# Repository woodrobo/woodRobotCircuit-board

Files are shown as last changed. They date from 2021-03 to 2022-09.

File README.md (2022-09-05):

# woodRobotCircuit-board
趣味でロボコン的なロボットを動かす回路を作ろうプロジェクト（？）の回路・基板リポジトリである。ファームウェアは[ここ](https://github.com/woodrobo/woodRobotCircuit-firmware/tree/kanojo_robo)。
ロボコンや趣味のロボット製作等の参考にどうぞ。  

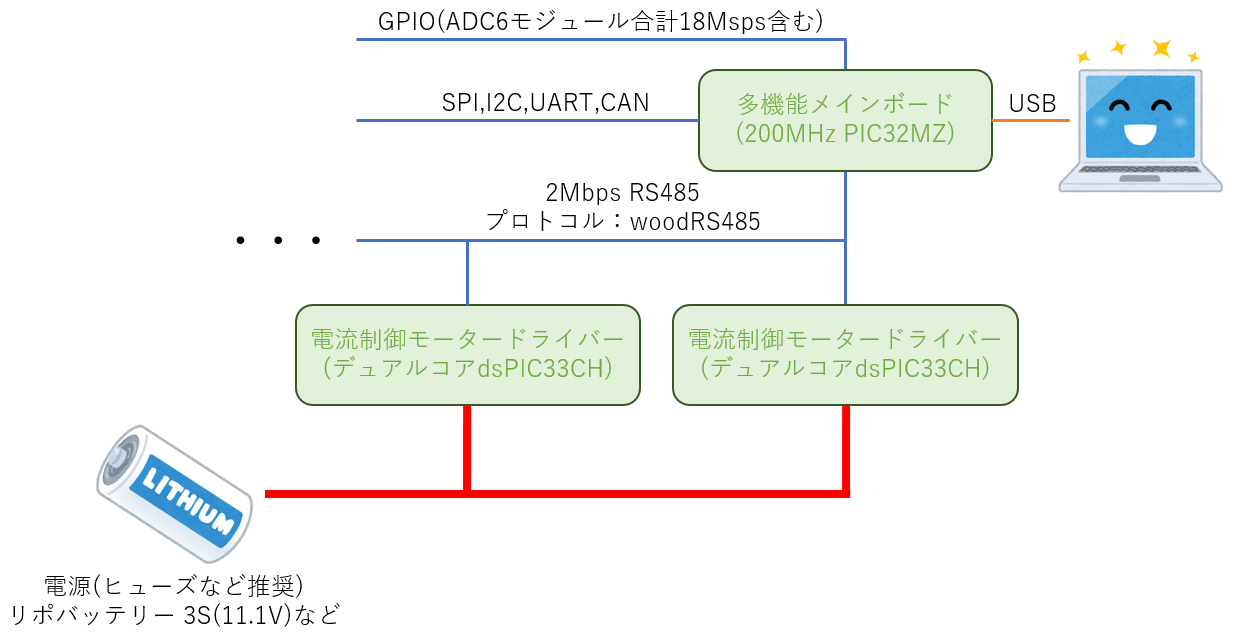
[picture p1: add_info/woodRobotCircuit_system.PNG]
システム概要
  
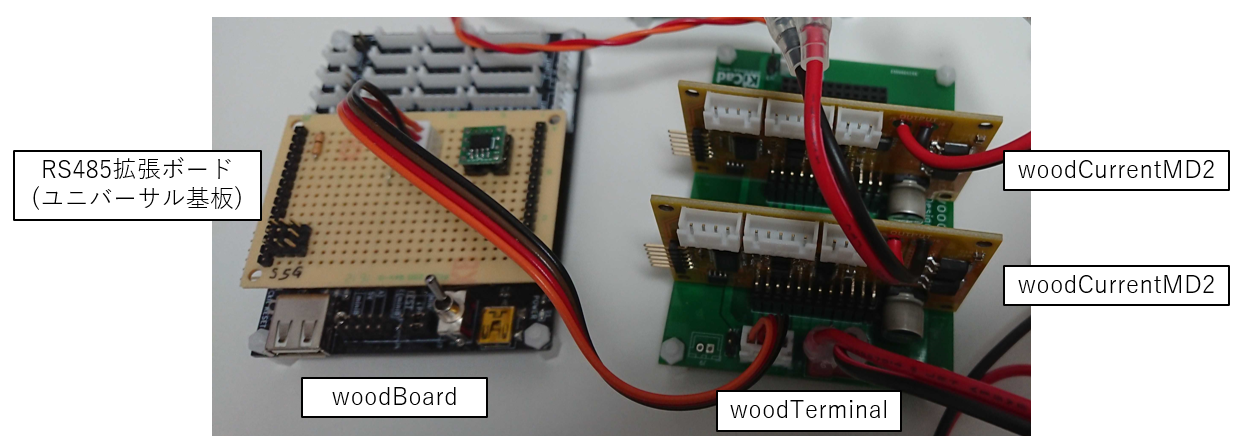
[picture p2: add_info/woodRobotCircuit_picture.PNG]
実際の基板たち
  

メインボードとモータードライバは2MbpsのRS485で接続されており、プロトコルはwoodRS485という独自規格を用いているが、これも[リポジトリ](https://github.com/woodrobo/wood_rs485)として公開されており、C言語が使用できるマイコンであればどのマイコンでも移植できるよう実装されている。  
モータードライバーは電流制御に対応しており高度な制御が可能となる。  

# 電流制御とは
モーターは一般に抵抗とコイル、そして回転速度に比例する逆起電力の3つが直列接続されたモデルで表現されます。  

$$ Vin = Ri + L\frac{di}{dt}+V$$

電子工作でよく使用されるPWM制御ではこの3つの要素全体にかける電圧を制御しているのでこれは直接的に物理的な意味を持ちません。モーターに流れる電流はトルクに比例すると言われこの電流を制御する電流制御方式ではトルクという物理量を直接的に扱うことができます。

$$ \tau = K_t i $$

製品や研究の世界ではこのトルク制御により運動方程式からモデルを立てて制御をすることが一般となっています。例えばロボティクスでは動力学や逆動力学によりロボットアームを制御しています。モデルに基づいた制御をするために電流制御は必須の機能です。

# 基板の簡単な紹介
woodBoard  
メインボードでありRS485以外にもSPI,I2C,UART,CANなどの通信ポートを備えている。また余った全てのGPIOをピンソケットに出しており、3MbpsのADCモジュールが6つ搭載されているため合計で18Mspsもの高速なAD変換を実現できる。もちろんこれはモジュール数であるのでAD変換可能なピン数はこれより多い。

woodTerminal  
モータードライバー基板などをまとめるための基板であり、1つのターミナル基板につきモータードライバー基板を5枚配置することができる。制御側の電源はRS485ポートの5V電源のほか、DCDCコンバータが搭載されているのでLiPo 3S(11.1V)等からも5Vを生成できる。
  
woodCurrentMD  
初期のモータードライバーであるが、ゲートドライバICが手に入らなかったことや回路トラブルにより闇の基板だぞ。

woodCurrentMD2  
20kHz電流制御モータードライバー。ロジック側とパワー側はフォトカプラで絶縁されており、モーター電流は磁気式の電流センサで計測している。UARTポート、エンコーダポート、ADCポートを搭載しており、また搭載しているマイコンはマルチプレクサにより自由にピン配置を変更できるため拡張性に優れる。180MHz/200MHzデュアルコアマイコンdsPIC33CHにより電流制御とその他処理をコアで分離するためプログラムの拡張性に優れる。  

# 基板発売について  
ここのサイトで基板のみを売ってるぞ！  
https://woodrobo.booth.pm/items/4136212

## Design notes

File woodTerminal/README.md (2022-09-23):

# woodTerminal
モータードライバーなどを5枚までまとめるターミナル基板

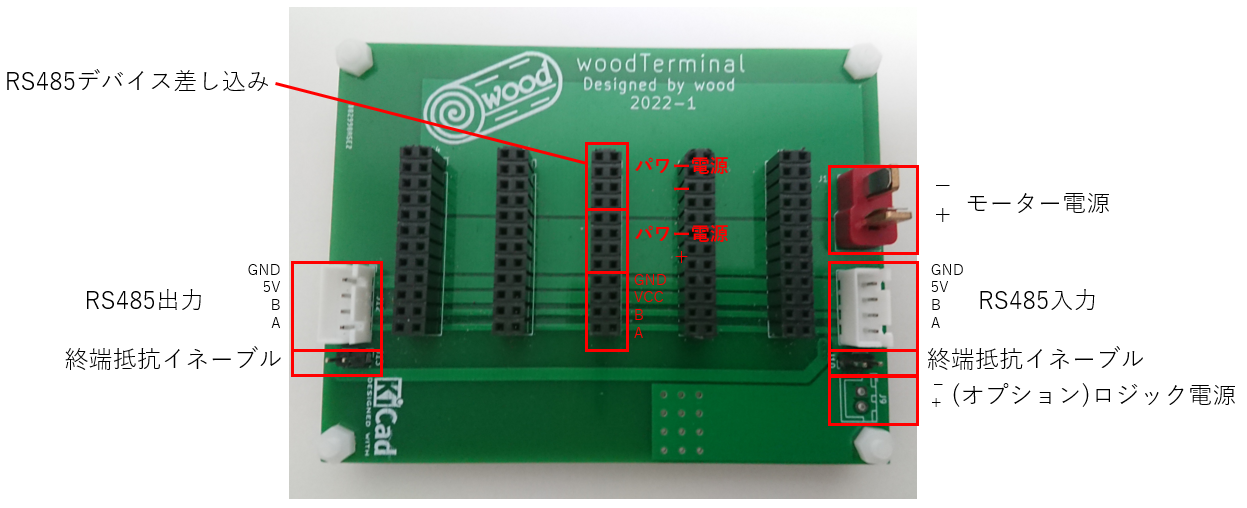
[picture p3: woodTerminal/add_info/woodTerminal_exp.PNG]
基板表

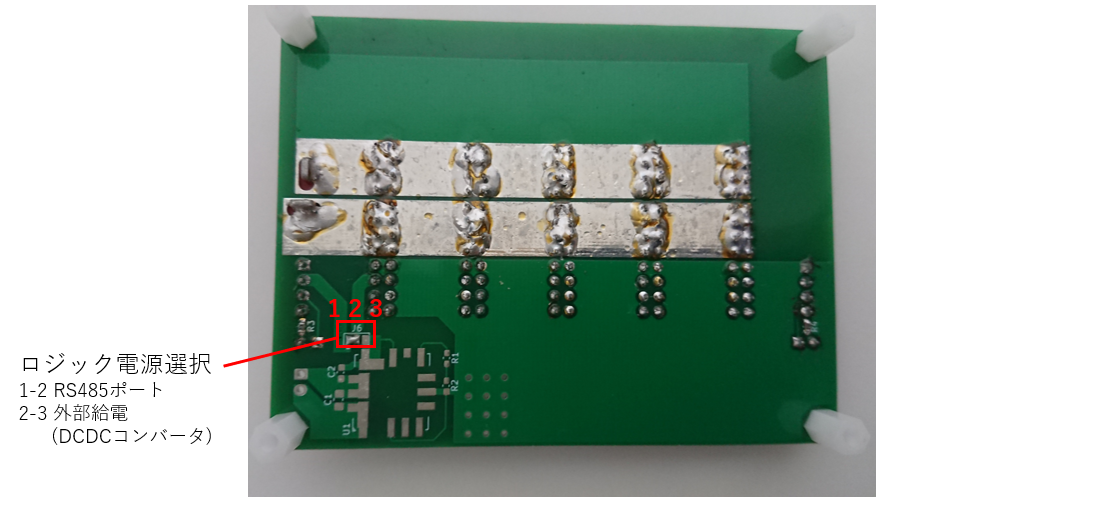
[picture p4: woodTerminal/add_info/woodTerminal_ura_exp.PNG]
基板裏
 

仕様
- ロジック側
	- RS485の4ピンポート(A,B,5V,GND)
		- RS485の終端抵抗は横にあるピンヘッダをショートすることで行う
	- 外部電源供給
		- LiPo3S(11.1V)などからDCDCコンバータを通して5Vを供給する(オプション)
	- 電源選択は基板裏面にあるパッドをショートして行う(4ピンコネクタor外部供給)
	- よく考えると外部供給は一度も試してない(ｶｽ)
- パワー側
	- Tコネクタ
  
  # 部品について  
  部品表.csvおよび部品個数表.csvを見てくれ。

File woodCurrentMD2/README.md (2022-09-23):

# woodCurrentMD2
2Mbps RS485対応電流制御DCモータードライバー

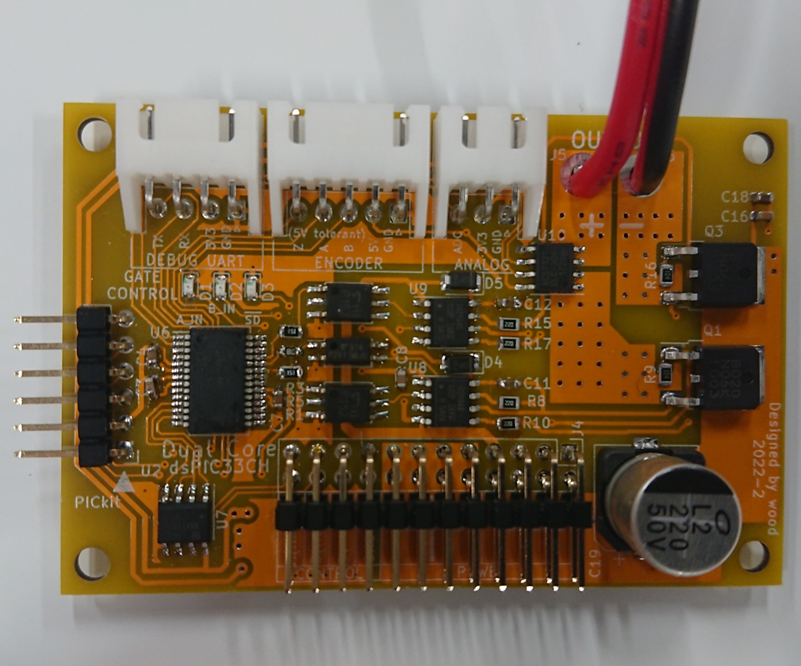
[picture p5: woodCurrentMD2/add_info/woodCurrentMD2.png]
基板表

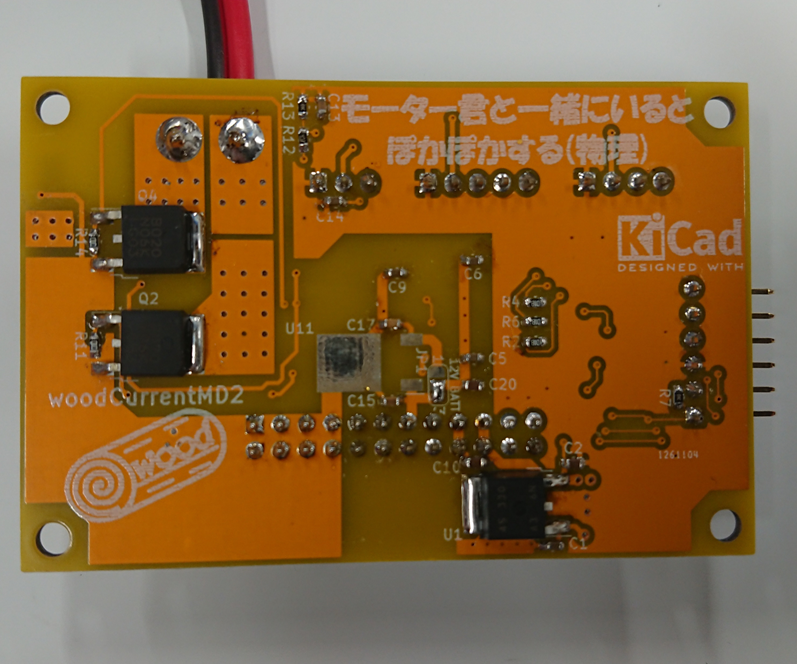
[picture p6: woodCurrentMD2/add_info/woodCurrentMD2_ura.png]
基板裏
  

仕様
- 通信規格2Mbps RS485
	- 受信：電圧制御(PWM値)、電流制御
	- 送信：電流値、AD変換ポートの値、エンコーダのカウント値
- woodTerminal接続端子
	- ロジック側とパワー側は絶縁されている
	- ロジック側：A, B, 5V, GND
	- パワー側　：VCC, GND
	- 詳細はwoodTerminalを参照の事
- 20kHz電流制御
- デバッグUARTポート
	- 現状RXから信号が出てる()
- インクリメンタル型エンコーダポート
	- PICのQEI機能でハードウェア処理
	- たぶん高速な波形も読める
	- Z相はファームウェアが現在対応してない、配線しないこと
- (ポテンショなどの)AD変換ポート

通信規格  
woodRS485で以下のデータをやり取りする。

**マイコンボード→モータードライバー**  
モードは0で電圧制御(PWM値)、1で電流制御を意味する。16bit値は16bitのsigned int型であり、電圧制御ではPWM値(-10000 ~ 10000)を指示し、電流制御では1当たり0.0179[A]となる。  
例えば、電圧制御PWM1000ならば「0,3,232」となる。電流制御1Aならば「1,0,56」(1.0024A)となる。

| バイト数 | データ |
----|---- 
| 1 | モード |
| 2 | 16bit値(上位バイト) |
| 3 | 16bit値(下位バイト) |

**モータードライバー→マイコンボード**  
電流値は16bitのsigned int型であり、1あたり0.0179[A]を意味する。AD変換ポートはAD変換値(12bit 0-4095)が入っている。 エンコーダは16bitのsigned int型である。(インクリメンタル型エンコーダは差分しか意味を持たないのでunsignedと解釈してもsignedと解釈しても同じ)

| バイト数 | データ |
----|---- 
| 1 | 電流値(上位バイト) |
| 2 | 電流値(下位バイト) |
| 3 | AD変換ポート(上位バイト) |
| 4 | AD変換ポート(下位バイト) |
| 5 | エンコーダ(上位バイト) |
| 6 | エンコーダ(下位バイト) |
  
  # 部品について  
  部品表.csvおよび部品個数表.csvを見てくれ。

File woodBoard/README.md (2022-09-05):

# woodBoard
ロボット回路のメインボード

趣味でロボコン的なロボットを動かす回路を作ろうプロジェクト（？）のメインボードである。  
PIC32MZを使用しており200MHz/330DMIPSらしい。（たぶん）  
woodBoardの特徴を説明すると  
- 通信ポートが豊富(アドレスが被っても安心設計)
    - CAN通信2ポート(各ポートに2つコネクタ搭載、終端抵抗ジャンパピンで設定可能)  
    - SPI通信2ポート(そのうち1つのポートはSS違いで4つコネクタ配置、もう1つはピンソケット)
    - I2C通信2ポート(そのうち1つのポートは4つコネクタ配置、もう1つはピンソケット)
    - UART5ポート(USBシリアルに1,通信ポートに2,ピンソケットに2)
- ほとんど秋月電子で部品購入可能
    - 一部は秋月電子で購入できないが
    - EHコネクタ->お好きなコネクタに変更
    - MCP2562->DIP品なら秋月電子で売っているのでピンソケットからCANTX,CANRXを取り出せば動作可能
    - 表面実装の24MHz水晶->スルーホール部品を"気合"または、違う周波数に変更する（ただしUSB通信をするには12MHzまたは24MHz）
  
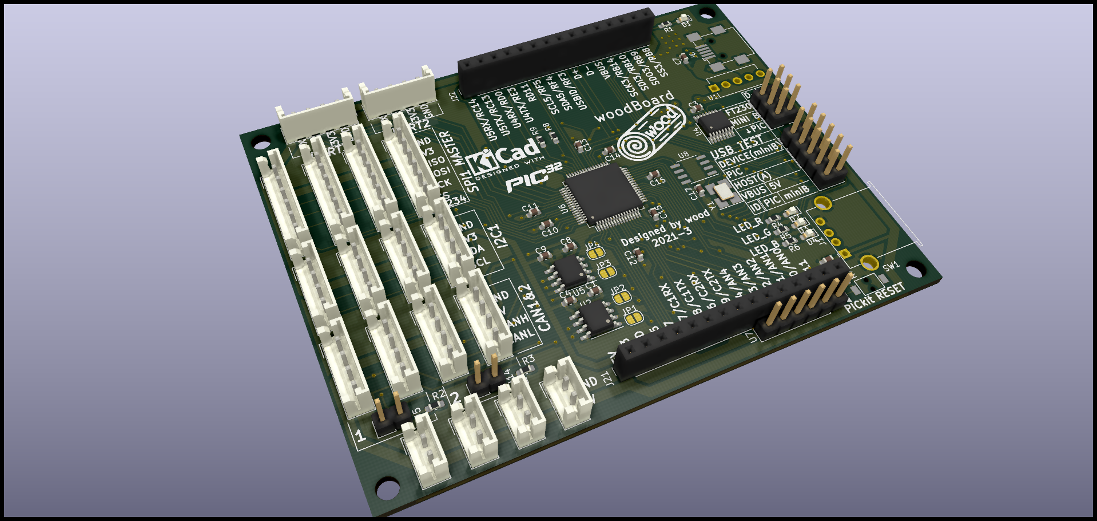
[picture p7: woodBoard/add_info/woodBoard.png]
基板表
    
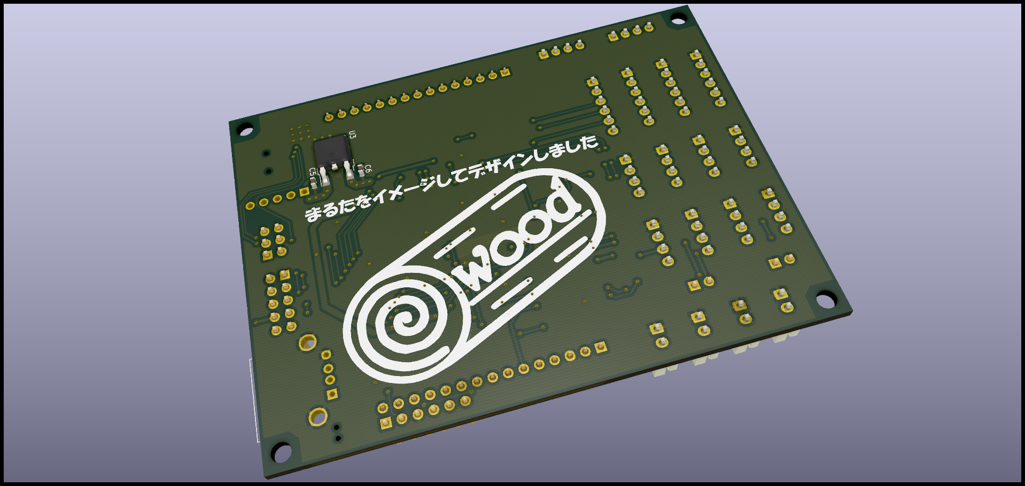
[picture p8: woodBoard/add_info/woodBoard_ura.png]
基板裏
    
  
# 部品について  
部品表.csvおよび部品個数表.csvを見てくれ。

# 基板ミス情報
- 「FT230XSの10番ピンである3V3OUT」-「GND」間に0.1uFのコンデンサを†気合い†で入れる必要がある。  
- 「NJM2391DL1-33」の出力側のコンデンサは積層セラミックコンデンサではなく電解コンデンサでなければならない。

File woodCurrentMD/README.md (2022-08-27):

# woodCurrentMD
電流制御モタドラを作ろうとした。  
後継プロジェクトはwoodCurrentMD2なので、そちらをご覧ください。

仕様
- PWMをフォトカプラに入れるとFETから煙が出る
- フルブリッジドライバのA3921が手に入らない

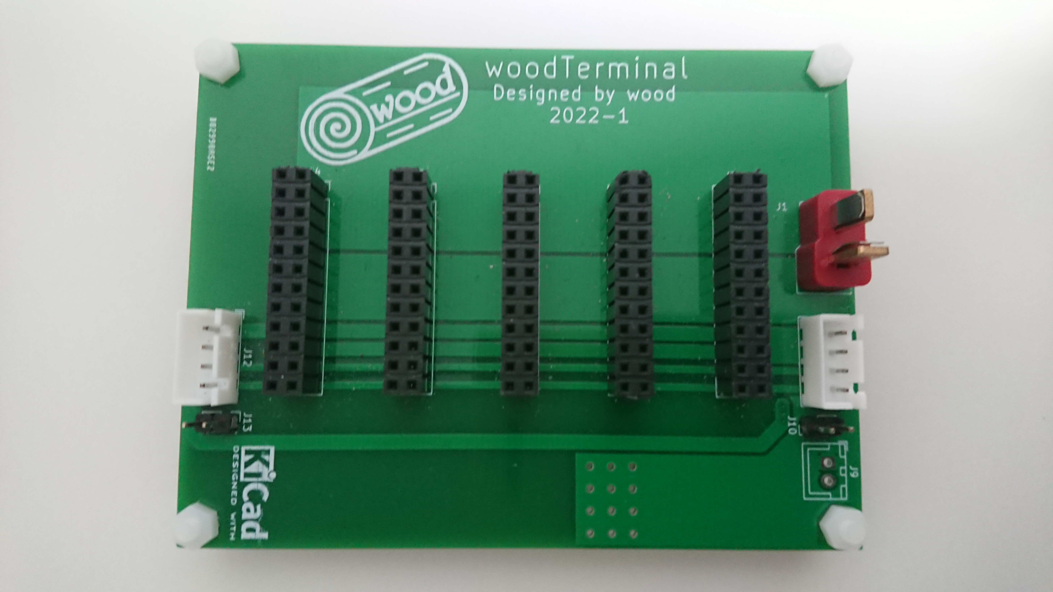
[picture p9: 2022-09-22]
woodTerminal/add_info/woodTerminal.JPG

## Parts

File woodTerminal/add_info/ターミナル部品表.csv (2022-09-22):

Reference | Value | Footprint | 説明
C1 | 22u | Capacitor_SMD:C_0805_2012Metric_Pad1.15x1.40mm_HandSolder | チップコンデンサ2012 22uF
C2 | 10u | Capacitor_SMD:C_0603_1608Metric_Pad1.05x0.95mm_HandSolder | チップコンデンサ1608 10uF
J1 | Conn_01x02 | Connector_JST:JST_XH_B2B-XH-A_1x02_P2.50mm_Vertical | XHコネクタ縦2ピン
J2 | Conn_01x04 | Connector_JST:JST_XH_B4B-XH-A_1x04_P2.50mm_Vertical | XHコネクタ縦4ピン
J3 | Conn_01x04 | Connector_JST:JST_XH_B4B-XH-A_1x04_P2.50mm_Vertical | XHコネクタ縦4ピン
J4 | Conn_01x02 | Connector_PinHeader_2.54mm:PinHeader_1x02_P2.54mm_Vertical | ピンヘッダ1×2ピン
J5 | Conn_01x02 | Connector_PinHeader_2.54mm:PinHeader_1x02_P2.54mm_Vertical | ピンヘッダ1×2ピン
J6 | Conn_01x02 | 0_kicad_wood:DeansTConnector_Male | Tコネクタ(オス)
J7 | Conn_01x03 | Jumper:SolderJumper-3_P1.3mm_Open_Pad1.0x1.5mm | 電源選択、どちらかをブリッジすること
J8 | Conn_02x12_Odd_Even | Connector_PinSocket_2.54mm:PinSocket_2x12_P2.54mm_Vertical | ピンソケット2×12
J9 | Conn_02x12_Odd_Even | Connector_PinSocket_2.54mm:PinSocket_2x12_P2.54mm_Vertical | ピンソケット2×12
J10 | Conn_02x12_Odd_Even | Connector_PinSocket_2.54mm:PinSocket_2x12_P2.54mm_Vertical | ピンソケット2×12
J11 | Conn_02x12_Odd_Even | Connector_PinSocket_2.54mm:PinSocket_2x12_P2.54mm_Vertical | ピンソケット2×12
J12 | Conn_02x12_Odd_Even | Connector_PinSocket_2.54mm:PinSocket_2x12_P2.54mm_Vertical | ピンソケット2×12
R1 | 120 | Resistor_SMD:R_0603_1608Metric_Pad1.05x0.95mm_HandSolder | チップ抵抗1608 120Ω
R2 | 120 | Resistor_SMD:R_0603_1608Metric_Pad1.05x0.95mm_HandSolder | チップ抵抗1608 120Ω
R3 | 1k | Resistor_SMD:R_0603_1608Metric_Pad1.05x0.95mm_HandSolder | チップ抵抗1608 1kΩ
R4 | 330 | Resistor_SMD:R_0603_1608Metric_Pad1.05x0.95mm_HandSolder | チップ抵抗1608 330Ω
U1 | DCDC_Converter_OKL | 0_kicad_wood:DCDC_Converter_OKL | DCDCコンバータ

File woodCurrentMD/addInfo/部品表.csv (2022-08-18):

Reference | Value | Footprint | 説明
C1 | 0.1u | Capacitor_SMD:C_0603_1608Metric | チップコンデンサ0.1uF 1608
C10 | 20u | Capacitor_SMD:C_0805_2012Metric | チップコンデンサ20uF 2012
C11 | 10u | Capacitor_SMD:C_0603_1608Metric | チップコンデンサ10uF 1608
C12 | 0.47u | Capacitor_SMD:C_0603_1608Metric | チップコンデンサ0.47uF 1608
C13 | 0.1u | Capacitor_SMD:C_0603_1608Metric | チップコンデンサ0.1uF 1608
C14 | 0.1u | Capacitor_SMD:C_0603_1608Metric | チップコンデンサ0.1uF 1608
C15 | 1n | Capacitor_SMD:C_0603_1608Metric | チップコンデンサ1nF 1608
C16 | 0.1u | Capacitor_SMD:C_0603_1608Metric | チップコンデンサ0.1uF 1608
C17 | 1u | Capacitor_SMD:C_0603_1608Metric | チップコンデンサ1uF 1608
C18 | 10u | Capacitor_SMD:C_0603_1608Metric | チップコンデンサ10uF 1608
C19 | 0.1u | Capacitor_SMD:C_0603_1608Metric | チップコンデンサ0.1uF 1608
C2 | 10u | Capacitor_SMD:C_0603_1608Metric | チップコンデンサ10uF 1608
C20 | 220u | Capacitor_SMD:CP_Elec_10x10 | チップ電解コンデンサ220uF 10×10mm
C3 | 0.1u | Capacitor_SMD:C_0603_1608Metric | チップコンデンサ0.1uF 1608
C4 | 0.1u | Capacitor_SMD:C_0603_1608Metric | チップコンデンサ0.1uF 1608
C5 | 0.1u | Capacitor_SMD:C_0603_1608Metric | チップコンデンサ0.1uF 1608
C6 | 0.1u | Capacitor_SMD:C_0603_1608Metric | チップコンデンサ0.1uF 1608
C7 | 0.1u | Capacitor_SMD:C_0603_1608Metric | チップコンデンサ0.1uF 1608
C8 | 0.1u | Capacitor_SMD:C_0603_1608Metric | チップコンデンサ0.1uF 1608
C9 | 0.1u | Capacitor_SMD:C_0603_1608Metric | チップコンデンサ0.1uF 1608
D1 | LED | LED_SMD:LED_0603_1608Metric | チップLED orange 1608
D2 | LED | LED_SMD:LED_0603_1608Metric | チップLED blue 1608
D3 | LED | LED_SMD:LED_0603_1608Metric | チップLED orange 1608
D4 | LED | LED_SMD:LED_0603_1608Metric | チップLED blue 1608
D5 | LED | LED_SMD:LED_0603_1608Metric | チップLED green 1608
D6 | LED | LED_SMD:LED_0603_1608Metric | チップLED green 1608
D7 | SS2040FL | Diode_SMD:D_1206_3216Metric | チップショットキーバリアダイオード
J1 | Conn_01x04 | Connector_JST:JST_XH_S4B-XH-A_1x04_P2.50mm_Horizontal | XHコネクタ横4ピン
J2 | Conn_01x05 | Connector_JST:JST_XH_S5B-XH-A_1x05_P2.50mm_Horizontal | XHコネクタ横5ピン
J3 | Conn_01x03 | Connector_JST:JST_XH_S3B-XH-A_1x03_P2.50mm_Horizontal | XHコネクタ横3ピン
J4 | Conn_02x12_Odd_Even | Connector_PinHeader_2.54mm:PinHeader_2x12_P2.54mm_Vertical | L字ピンヘッダ 2.54mm 2x12
J5 | Conn_01x01 | MountingHole:MountingHole_2.2mm_M2_Pad | 配線つける端子
J6 | Conn_01x01 | MountingHole:MountingHole_2.2mm_M2_Pad | 配線つける端子
Q1 | Q_NMOS_GDS | Package_TO_SOT_SMD:TO-252-2 | NchMOSFET NP52N06SLG
Q2 | Q_NMOS_GDS | Package_TO_SOT_SMD:TO-252-2 | NchMOSFET NP52N06SLG
Q3 | Q_NMOS_GDS | Package_TO_SOT_SMD:TO-252-2 | NchMOSFET NP52N06SLG
Q4 | Q_NMOS_GDS | Package_TO_SOT_SMD:TO-252-2 | NchMOSFET NP52N06SLG
R1 | 1k | Resistor_SMD:R_0603_1608Metric | チップ抵抗1kΩ 1608
R10 | 10k | Resistor_SMD:R_0603_1608Metric | チップ抵抗10kΩ 1608
R11 | 10k | Resistor_SMD:R_0603_1608Metric | チップ抵抗10kΩ 1608
R12 | 3.3k | Resistor_SMD:R_0603_1608Metric | チップ抵抗3.3kΩ 1608
R13 | 3.3k | Resistor_SMD:R_0603_1608Metric | チップ抵抗3.3kΩ 1608
R14 | 10k | Resistor_SMD:R_0603_1608Metric | チップ抵抗10kΩ 1608
R15 | 1k | Resistor_SMD:R_0603_1608Metric | チップ抵抗1kΩ 1608
R16 | 1k | Resistor_SMD:R_0603_1608Metric | チップ抵抗1kΩ 1608
R17 | 20 | Resistor_SMD:R_0603_1608Metric | チップ抵抗20Ω 1608
R18 | 20 | Resistor_SMD:R_0603_1608Metric | チップ抵抗20Ω 1608
R19 | 4.7k | Resistor_SMD:R_0603_1608Metric | チップ抵抗4.7kΩ 1608
R2 | 1k | Resistor_SMD:R_0603_1608Metric | チップ抵抗1kΩ 1608
R20 | 10k | Resistor_SMD:R_0603_1608Metric | チップ抵抗10kΩ 1608
R21 | 20 | Resistor_SMD:R_0603_1608Metric | チップ抵抗20Ω 1608
R22 | 20 | Resistor_SMD:R_0603_1608Metric | チップ抵抗20Ω 1608
R3 | 1k | Resistor_SMD:R_0603_1608Metric | チップ抵抗1kΩ 1608
R4 | 1k | Resistor_SMD:R_0603_1608Metric | チップ抵抗1kΩ 1608
R5 | 1k | Resistor_SMD:R_0603_1608Metric | チップ抵抗1kΩ 1608
R6 | 1k | Resistor_SMD:R_0603_1608Metric | チップ抵抗1kΩ 1608
R7 | 1k | Resistor_SMD:R_0603_1608Metric | チップ抵抗1kΩ 1608
R8 | 1k | Resistor_SMD:R_0603_1608Metric | チップ抵抗1kΩ 1608
R9 | 10k | Resistor_SMD:R_0603_1608Metric | チップ抵抗10kΩ 1608
U1 | NJM2845 | Package_TO_SOT_SMD:TO-252-2 | 3端子レギュレータ NJM2845
U10 | A3921 | Package_SO:HTSSOP-28-1EP_4.4x9.7mm_P0.65mm_EP2.85x5.4mm | フルブリッジドライバ A3921
U11 | ACS712xLCTR-30A | Package_SO:SOIC-8_3.9x4.9mm_P1.27mm | 電流センサ ACS712ELCTR-30A-T
U2 | PICkit3 | Connector_PinHeader_2.54mm:PinHeader_1x06_P2.54mm_Horizontal | L字ピンヘッダ 2.54mm 1x6
U3 | TLP291 | Package_SO:SOIC-4_4.55x2.6mm_P1.27mm | フォトカプラ TLP291
U4 | TLP2361 | Package_SO:SO-6_4.4x3.6mm_P1.27mm | フォトカプラ TLP2361
U5 | TLP2361 | Package_SO:SO-6_4.4x3.6mm_P1.27mm | フォトカプラ TLP2361
U6 | TLP2361 | Package_SO:SO-6_4.4x3.6mm_P1.27mm | フォトカプラ TLP2361
U7 | dsPIC33CH64MP202T | Package_SO:SSOP-28_5.3x10.2mm_P0.65mm | dsPIC33CH64MP202T-I/SS
U8 | MAX3485 | Package_SO:SOIC-8_3.9x4.9mm_P1.27mm | 3.3V動作RS485ドライバ MAX3485ED
U9 | TC7WU04Fx | Package_SO:SSOP-8_2.95x2.8mm_P0.65mm | 3回路インバーター TC7WU04FU

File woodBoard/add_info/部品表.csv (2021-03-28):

Reference | Value | Footprint | 説明
C1 | 0.1u | Capacitor_SMD:C_0603_1608Metric | チップコンデンサ0.1uF 1005
C2 | 0.1u | Capacitor_SMD:C_0603_1608Metric | チップコンデンサ0.1uF 1005
C3 | 0.1u | Capacitor_SMD:C_0603_1608Metric | チップコンデンサ0.1uF 1005
C4 | 0.1u | Capacitor_SMD:C_0603_1608Metric | チップコンデンサ0.1uF 1005
C5 | 0.1u | Capacitor_SMD:C_0603_1608Metric | チップコンデンサ0.1uF 1005
C6 | 10u | Capacitor_SMD:C_0603_1608Metric_Pad1.05x0.95mm_HandSolder | チップコンデンサ10uF 1608
C7 | 0.1u | Capacitor_SMD:C_0603_1608Metric | チップコンデンサ0.1uF 1005
C8 | 0.1u | Capacitor_SMD:C_0603_1608Metric | チップコンデンサ0.1uF 1005
C9 | 0.1u | Capacitor_SMD:C_0603_1608Metric | チップコンデンサ0.1uF 1005
C10 | 0.1u | Capacitor_SMD:C_0603_1608Metric | チップコンデンサ0.1uF 1005
C11 | 0.1u | Capacitor_SMD:C_0603_1608Metric | チップコンデンサ0.1uF 1005
C12 | 0.1u | Capacitor_SMD:C_0603_1608Metric | チップコンデンサ0.1uF 1005
C13 | 0.1u | Capacitor_SMD:C_0603_1608Metric | チップコンデンサ0.1uF 1005
C14 | 0.1u | Capacitor_SMD:C_0603_1608Metric | チップコンデンサ0.1uF 1005
C15 | 0.1u | Capacitor_SMD:C_0603_1608Metric | チップコンデンサ0.1uF 1005
C16 | 0.1u | Capacitor_SMD:C_0603_1608Metric | チップコンデンサ0.1uF 1005
C17 | 0.1u | Capacitor_SMD:C_0603_1608Metric | チップコンデンサ0.1uF 1005
D1 | LED | LED_SMD:LED_0603_1608Metric_Pad1.05x0.95mm_HandSolder | チップLED red 1608
D2 | LED | LED_SMD:LED_0603_1608Metric_Pad1.05x0.95mm_HandSolder | チップLED red 1608
D3 | LED | LED_SMD:LED_0603_1608Metric_Pad1.05x0.95mm_HandSolder | チップLED green 1608
D4 | LED | LED_SMD:LED_0603_1608Metric_Pad1.05x0.95mm_HandSolder | チップLED blue 1608
J1 | USB_A | Connector_USB:USB_A_Stewart_SS-52100-001_Horizontal | USB A
J2 | Conn_01x04 | Connector_JST:JST_EH_B4B-EH-A_1x04_P2.50mm_Vertical | EHコネクタ縦4ピン
J3 | Conn_01x04 | Connector_JST:JST_EH_B4B-EH-A_1x04_P2.50mm_Vertical | EHコネクタ縦4ピン
J4 | Conn_02x05_Odd_Even | Connector_PinHeader_2.54mm:PinHeader_2x05_P2.54mm_Vertical | ピンヘッダ 2.54mm 2x5
J5 | Conn_01x02 | Connector_PinHeader_2.54mm:PinHeader_1x02_P2.54mm_Vertical | ピンヘッダ 2.54mm 1x2
J6 | USB_B_Mini | Connector_USB:USB_Mini-B_Wuerth_65100516121_Horizontal | USB Bミニ
J7 | Conn_02x03_Odd_Even | Connector_PinHeader_2.54mm:PinHeader_2x03_P2.54mm_Vertical | ピンヘッダ 2.54mm 2x3
J8 | Conn_01x04 | Connector_JST:JST_EH_B4B-EH-A_1x04_P2.50mm_Vertical | EHコネクタ縦4ピン
J9 | Conn_01x04 | Connector_JST:JST_EH_B4B-EH-A_1x04_P2.50mm_Vertical | EHコネクタ縦4ピン
J10 | Conn_01x02 | Connector_JST:JST_EH_B2B-EH-A_1x02_P2.50mm_Vertical | EHコネクタ縦2ピン
J11 | Conn_01x02 | Connector_JST:JST_EH_B2B-EH-A_1x02_P2.50mm_Vertical | EHコネクタ縦2ピン
J12 | Conn_01x02 | Connector_JST:JST_EH_B2B-EH-A_1x02_P2.50mm_Vertical | EHコネクタ縦2ピン
J13 | Conn_01x02 | Connector_JST:JST_EH_B2B-EH-A_1x02_P2.50mm_Vertical | EHコネクタ縦2ピン
J14 | Conn_01x02 | Connector_PinHeader_2.54mm:PinHeader_1x02_P2.54mm_Vertical | ピンヘッダ 2.54mm 1x2
J15 | Conn_01x04 | Connector_JST:JST_EH_B4B-EH-A_1x04_P2.50mm_Vertical | EHコネクタ縦4ピン
J16 | Conn_01x04 | Connector_JST:JST_EH_B4B-EH-A_1x04_P2.50mm_Vertical | EHコネクタ縦4ピン
J17 | Conn_01x06 | Connector_JST:JST_EH_B6B-EH-A_1x06_P2.50mm_Vertical | EHコネクタ縦6ピン
J18 | Conn_01x06 | Connector_JST:JST_EH_B6B-EH-A_1x06_P2.50mm_Vertical | EHコネクタ縦6ピン
J19 | Conn_01x06 | Connector_JST:JST_EH_B6B-EH-A_1x06_P2.50mm_Vertical | EHコネクタ縦6ピン
J20 | Conn_01x06 | Connector_JST:JST_EH_B6B-EH-A_1x06_P2.50mm_Vertical | EHコネクタ縦6ピン
J21 | Conn_01x15 | Connector_PinSocket_2.54mm:PinSocket_1x15_P2.54mm_Vertical | ピンソケット 2.54mm 1x15
J22 | Conn_01x15 | Connector_PinSocket_2.54mm:PinSocket_1x15_P2.54mm_Vertical | ピンソケット 2.54mm 1x15
J23 | Conn_01x04 | Connector_JST:JST_EH_B4B-EH-A_1x04_P2.50mm_Vertical | EHコネクタ縦4ピン
J24 | Conn_01x04 | Connector_JST:JST_EH_B4B-EH-A_1x04_P2.50mm_Vertical | EHコネクタ縦4ピン
J25 | Conn_01x04 | Connector_JST:JST_EH_B4B-EH-A_1x04_P2.50mm_Vertical | EHコネクタ縦4ピン
J26 | Conn_01x04 | Connector_JST:JST_EH_B4B-EH-A_1x04_P2.50mm_Vertical | EHコネクタ縦4ピン
JP1 | SolderJumper_2_Open | Jumper:SolderJumper-2_P1.3mm_Open_RoundedPad1.0x1.5mm | 部品無し(用途に応じてはんだ付け)
JP2 | SolderJumper_2_Open | Jumper:SolderJumper-2_P1.3mm_Open_RoundedPad1.0x1.5mm | 部品無し(用途に応じてはんだ付け)
JP3 | SolderJumper_2_Open | Jumper:SolderJumper-2_P1.3mm_Open_RoundedPad1.0x1.5mm | 部品無し(用途に応じてはんだ付け)
JP4 | SolderJumper_2_Open | Jumper:SolderJumper-2_P1.3mm_Open_RoundedPad1.0x1.5mm | 部品無し(用途に応じてはんだ付け)
R1 | 1k | Resistor_SMD:R_0603_1608Metric_Pad1.05x0.95mm_HandSolder | チップ抵抗 1kΩ 1608
R2 | 120 | Resistor_SMD:R_0603_1608Metric_Pad1.05x0.95mm_HandSolder | チップ抵抗 120 1608
R3 | 120 | Resistor_SMD:R_0603_1608Metric_Pad1.05x0.95mm_HandSolder | チップ抵抗 120 1608
R4 | 1k | Resistor_SMD:R_0603_1608Metric_Pad1.05x0.95mm_HandSolder | チップ抵抗 1kΩ 1608
R5 | 1k | Resistor_SMD:R_0603_1608Metric_Pad1.05x0.95mm_HandSolder | チップ抵抗 1kΩ 1608
R6 | 1k | Resistor_SMD:R_0603_1608Metric_Pad1.05x0.95mm_HandSolder | チップ抵抗 1kΩ 1608
R7 | 10k | Resistor_SMD:R_0603_1608Metric_Pad1.05x0.95mm_HandSolder | チップ抵抗 10kΩ 1608
R8 | 1k | Resistor_SMD:R_0603_1608Metric_Pad1.05x0.95mm_HandSolder | チップ抵抗 1kΩ 1608
R9 | 1k | Resistor_SMD:R_0603_1608Metric_Pad1.05x0.95mm_HandSolder | チップ抵抗 1kΩ 1608
SW1 | SW_Push | 0_kicad_wood:SW_TVAF06-A020B-R | プッシュスイッチ 表面実装
U1 | SW_TOGGLE_2MOUNTINGHOLE | 0_kicad_wood:SW_2MS1T1B4VS2QES | トグルスイッチ スルーホール
U2 | MCP2562-E-SN | Package_SO:SOIC-8_3.9x4.9mm_P1.27mm | CANトランシーバ MCP2562
U3 | 3terminal_regulator(NJM2391DL1-33) | Package_TO_SOT_SMD:TO-252-2 | 3端子レギュレータ 表面実装
U4 | FT230XS | Package_SO:QSOP-16_3.9x4.9mm_P0.635mm | USBシリアル FT230XS
U5 | MCP2562-E-SN | Package_SO:SOIC-8_3.9x4.9mm_P1.27mm | CANトランシーバ MCP2562
U6 | PIC32MZ2048EFH064 | Package_QFP:TQFP-64_10x10mm_P0.5mm | マイコン PIC32MZ2048EFH064
U7 | PICkit3 | Connector_PinHeader_2.54mm:PinHeader_1x06_P2.54mm_Horizontal | L字ピンヘッダ 2.54mm 1x6
U8 | NJU6319AE | Package_SO:SO-8_3.9x4.9mm_P1.27mm | 水晶発振器用IC NJU6319AE
Y1 | Crystal_GND24 | Crystal:Crystal_SMD_SeikoEpson_FA238V-4Pin_3.2x2.5mm_HandSoldering | 水晶 24MHz 表面実装

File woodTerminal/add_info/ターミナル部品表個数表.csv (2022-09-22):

部品名 | 価格 | 個数 | 合計 | サイト | 備考、代替品など
チップコンデンサ2012 22uF | 12 | 1 | 12 | https://akizukidenshi.com/catalog/g/gP-08240/
チップコンデンサ1608 10uF | 15 | 1 | 15 | https://akizukidenshi.com/catalog/g/gP-13161/
XHコネクタ縦2ピン | 10 | 1 | 10 | https://akizukidenshi.com/catalog/g/gC-12247/
XHコネクタ縦4ピン | 10 | 2 | 20 | https://akizukidenshi.com/catalog/g/gC-12249/
ピンヘッダ1×2ピン | 1.75 | 2 | 3.5 | https://akizukidenshi.com/catalog/g/gC-00167/
Tコネクタ(オス) | 50 | 1 | 50 | https://akizukidenshi.com/catalog/g/gC-13420/
ピンソケット2×12 | 28.57 | 5 | 142.85 | https://akizukidenshi.com/catalog/g/gC-05780/
チップ抵抗1608 120Ω | 0.2 | 2 | 0.4 | https://akizukidenshi.com/catalog/g/gR-06121/
チップ抵抗1608 1kΩ | 0.2 | 1 | 0.2 | https://akizukidenshi.com/catalog/g/gR-14122/
チップ抵抗1608 330Ω | 0.2 | 1 | 0.2 | https://akizukidenshi.com/catalog/g/gR-16125/
DCDCコンバータ |  | 1 | 0 | 消滅 | OKL-T3-W12N-Cを頑張って探す(RS485ポート供給モードなら無くてもいい)
 |  |  | 254.15
#NAME?

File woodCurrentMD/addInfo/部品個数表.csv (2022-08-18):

部品名 | 価格 | 個数 | 合計 | サイト
チップコンデンサ0.1uF 1608 | 2 | 12 | 24 | https://akizukidenshi.com/catalog/g/gP-06166/
チップコンデンサ20uF 2012 | 12 | 1 | 12 | https://akizukidenshi.com/catalog/g/gP-08240/
チップコンデンサ10uF 1608 | 15 | 3 | 45 | https://akizukidenshi.com/catalog/g/gP-13161/
チップコンデンサ0.47uF 1608 | 7.25 | 1 | 7.25 | https://jp.rs-online.com/web/p/mlccs-multilayer-ceramic-capacitors/1843488
チップコンデンサ1nF 1608 | 2 | 1 | 2 | https://akizukidenshi.com/catalog/g/gP-14581/
チップコンデンサ1uF 1608 | 5 | 1 | 5 | https://akizukidenshi.com/catalog/g/gP-14526/
チップ電解コンデンサ220uF 10×10mm | 20 | 1 | 20 | https://akizukidenshi.com/catalog/g/gP-04577/
チップLED orange 1608 | 10 | 2 | 20 | https://akizukidenshi.com/catalog/g/gI-06416/
チップLED blue 1608 | 10 | 2 | 20 | https://akizukidenshi.com/catalog/g/gI-03982/
チップLED green 1608 | 12.5 | 2 | 25 | https://akizukidenshi.com/catalog/g/gI-06417/
チップショットキーバリアダイオード | 15 | 1 | 15 | https://akizukidenshi.com/catalog/g/gI-02073/
XHコネクタ横4ピン | 12 | 1 | 12 | https://akizukidenshi.com/catalog/g/gC-12842/
XHコネクタ横5ピン | 15 | 1 | 15 | https://akizukidenshi.com/catalog/g/gC-12428/
XHコネクタ横3ピン | 10 | 1 | 10 | https://akizukidenshi.com/catalog/g/gC-12263/
L字ピンヘッダ 2.54mm 2x12 | 30 | 1 | 30 | https://akizukidenshi.com/catalog/g/gC-00148/
配線つける端子 | 0 | 2 | 0 | お好きなように
NchMOSFET NP52N06SLG | 20 | 4 | 80 | https://akizukidenshi.com/catalog/g/gI-09928/
チップ抵抗1kΩ 1608 | 0.2 | 10 | 2 | https://akizukidenshi.com/catalog/g/gR-14122/
チップ抵抗10kΩ 1608 | 0.2 | 5 | 1 | https://akizukidenshi.com/catalog/g/gR-15029/
チップ抵抗3.3kΩ 1608 | 0.2 | 2 | 0.4 | https://akizukidenshi.com/catalog/g/gR-14661/
チップ抵抗20Ω 1608 | 0.2 | 4 | 0.8 | https://jp.rs-online.com/web/p/surface-mount-resistors/1995493
チップ抵抗4.7kΩ 1608 | 0.2 | 1 | 0.2 | https://akizukidenshi.com/catalog/g/gR-14121/
3端子レギュレータ NJM2845 | 50 | 1 | 50 | https://akizukidenshi.com/catalog/g/gI-11299/
フルブリッジドライバ A3921 | 350 | 1 | 350 | https://akizukidenshi.com/catalog/g/gI-12293/
電流センサ ACS712ELCTR-30A-T | 350 | 1 | 350 | https://akizukidenshi.com/catalog/g/gI-12292/
L字ピンヘッダ 2.54mm 1x6 | 7.5 | 1 | 7.5 | https://akizukidenshi.com/catalog/g/gC-01627/
フォトカプラ TLP291 | 20 | 1 | 20 | https://akizukidenshi.com/catalog/g/gI-07189/
フォトカプラ TLP2361 | 50 | 3 | 150 | https://akizukidenshi.com/catalog/g/gI-11004/
dsPIC33CH64MP202T-I/SS | 400 | 1 | 400 | https://akizukidenshi.com/catalog/g/gI-15250/
3.3V動作RS485ドライバ MAX3485ED | 70 | 1 | 70 | https://akizukidenshi.com/catalog/g/gI-16211/
3回路インバーター TC7WU04FU | 30 | 1 | 30 | https://akizukidenshi.com/catalog/g/gI-10462/
 |  |  | 1774.15

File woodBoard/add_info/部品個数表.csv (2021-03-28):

部品名 | 価格 | 個数 | 合計 | サイト
チップコンデンサ0.1uF 1005 | 1 | 16 | 16 | https://akizukidenshi.com/catalog/g/gP-13396/
チップコンデンサ10uF 1608 | 15 | 1 | 15 | https://akizukidenshi.com/catalog/g/gP-13161/
チップLED red 1608 | 10 | 2 | 20 | https://akizukidenshi.com/catalog/g/gI-03978/
チップLED green 1608 | 12.5 | 1 | 12.5 | https://akizukidenshi.com/catalog/g/gI-06417/
チップLED blue 1608 | 10 | 1 | 10 | https://akizukidenshi.com/catalog/g/gI-03982/
USB A | 50 | 1 | 50 | https://akizukidenshi.com/catalog/g/gC-11551/
USB Bミニ | 50 | 1 | 50 | https://akizukidenshi.com/catalog/g/gC-05843/
ピンヘッダ 2.54mm 1x2 | 1.75 | 2 | 3.5 | https://akizukidenshi.com/catalog/g/gC-00167/
L型ピンヘッダ 2.54mm 1x6 | 5.25 | 1 | 7.5 | https://akizukidenshi.com/catalog/g/gC-01627/
ピンヘッダ 2.54mm 2x3 | 3.75 | 1 | 3.75 | https://akizukidenshi.com/catalog/g/gC-00082/
ピンヘッダ 2.54mm 2x5 | 6.25 | 1 | 6.25 | https://akizukidenshi.com/catalog/g/gC-00082/
ピンソケット 2.54mm 1x15 | 40 | 2 | 80 | https://akizukidenshi.com/catalog/g/gC-10102/
EHコネクタ縦2ピン | 16.4 | 4 | 65.6 | https://www.monotaro.com/p/0071/4087/?t.q=EH%83R%83l%83N%83%5E
EHコネクタ縦4ピン | 27.4 | 10 | 274 | https://www.monotaro.com/p/0071/4218/?t.q=EH%83R%83l%83N%83%5E
EHコネクタ縦6ピン | 36.2 | 4 | 144.8 | https://www.monotaro.com/p/0071/4254/?t.q=EH%83R%83l%83N%83%5E
チップ抵抗 120 1608 | 0.2 | 2 | 0.4 | https://akizukidenshi.com/catalog/g/gR-06121/
チップ抵抗 1kΩ 1608 | 0.2 | 6 | 1.2 | https://akizukidenshi.com/catalog/g/gR-14122/
チップ抵抗 10kΩ 1608 | 0.2 | 1 | 0.2 | https://akizukidenshi.com/catalog/g/gR-06103/
プッシュスイッチ 表面実装 | 22 | 1 | 22 | https://akizukidenshi.com/catalog/g/gP-14888/
トグルスイッチ スルーホール | 80 | 1 | 80 | https://akizukidenshi.com/catalog/g/gP-00300/
CANトランシーバ MCP2562 | 118.91 | 2 | 237.82 | https://jp.rs-online.com/web/p/can-interface-ics/7990228/
3端子レギュレータ 表面実装 | 50 | 1 | 50 | https://akizukidenshi.com/catalog/g/gI-02252/
USBシリアル FT230XS | 220 | 1 | 220 | https://akizukidenshi.com/catalog/g/gI-13311/
マイコン PIC32MZ2048EFH064 | 1100 | 1 | 1100 | https://akizukidenshi.com/catalog/g/gI-13286/
水晶発振器用IC NJU6319AE | 25 | 1 | 25 | https://akizukidenshi.com/catalog/g/gI-10494/
水晶 24MHz 表面実装 | 63.58 | 1 | 63.58 | https://jp.rs-online.com/web/p/crystal-units/8136172/
 |  | 合計 | 2559.1

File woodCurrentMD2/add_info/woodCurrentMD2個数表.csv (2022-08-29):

部品名 | 価格 | 個数 | 合計 | サイト | 備考、代替品など
チップコンデンサ0.1uF 1608 | 2 | 11 | 22 | https://akizukidenshi.com/catalog/g/gP-06166/
チップコンデンサ10uF 1608 | 15 | 4 | 60 | https://akizukidenshi.com/catalog/g/gP-13161/
チップコンデンサ1nF 1608 | 2 | 1 | 2 | https://akizukidenshi.com/catalog/g/gP-14581/
チップコンデンサ1uF 1608 | 5 | 3 | 15 | https://akizukidenshi.com/catalog/g/gP-14526/
チップ電解コンデンサ220uF 10×10mm | 20 | 1 | 20 | https://akizukidenshi.com/catalog/g/gP-04577/
チップLED orange 1608 | 10 | 1 | 10 | https://akizukidenshi.com/catalog/g/gI-06416/
チップLED red 1608 | 10 | 1 | 10 | https://akizukidenshi.com/catalog/g/gI-03978/
チップLED green 1608 | 12.5 | 1 | 12.5 | https://akizukidenshi.com/catalog/g/gI-06417/
チップショットキーバリアダイオード | 15 | 2 | 30 | https://akizukidenshi.com/catalog/g/gI-02073/
XHコネクタ横4ピン | 12 | 1 | 12 | https://akizukidenshi.com/catalog/g/gC-12842/
XHコネクタ横5ピン | 15 | 1 | 15 | https://akizukidenshi.com/catalog/g/gC-12428/
XHコネクタ横3ピン | 10 | 1 | 10 | https://akizukidenshi.com/catalog/g/gC-12263/
L字ピンヘッダ 2.54mm 2x12 | 30 | 1 | 30 | https://akizukidenshi.com/catalog/g/gC-00148/
配線つける端子 | 0 | 2 | 0 | お好きなように
NchMOSFET MTB020N06KJ3 | 40 | 4 | 160 | https://akizukidenshi.com/catalog/g/gI-17075/
チップ抵抗150Ω 1608 | 0.2 | 2 | 0.4 | https://akizukidenshi.com/catalog/g/gR-06151/
チップ抵抗1kΩ 1608 | 0.2 | 4 | 0.8 | https://akizukidenshi.com/catalog/g/gR-14122/
チップ抵抗10kΩ 1608 | 0.2 | 2 | 0.4 | https://akizukidenshi.com/catalog/g/gR-15029/
チップ抵抗20Ω 1608 | 1 | 4 | 4 | https://jp.rs-online.com/web/p/surface-mount-resistors/1995493
チップ抵抗100kΩ 1608 | 0.2 | 4 | 0.8 | https://akizukidenshi.com/catalog/g/gR-15321/
チップ抵抗4.7kΩ 1608 | 0.2 | 1 | 0.2 | https://akizukidenshi.com/catalog/g/gR-14121/
3端子レギュレータ NJM2845 | 50 | 1 | 50 | https://akizukidenshi.com/catalog/g/gI-11299/
L字ピンヘッダ 2.54mm 1x6 | 7.5 | 1 | 7.5 | https://akizukidenshi.com/catalog/g/gC-01627/
フォトカプラ TLP291 | 20 | 1 | 20 | https://akizukidenshi.com/catalog/g/gI-07189/ | ほぼ互換品：https://akizukidenshi.com/catalog/g/gI-16298/
フォトカプラ TLP152 | 80 | 2 | 160 | https://akizukidenshi.com/catalog/g/gI-10824/
dsPIC33CH64MP202T-I/SS | 400 | 1 | 400 | https://akizukidenshi.com/catalog/g/gI-15250/
3.3V動作RS485ドライバ MAX3485ED | 70 | 1 | 70 | https://akizukidenshi.com/catalog/g/gI-16211/
ハーフブリッジドライバ IR2104 | 85 | 2 | 170 | https://akizukidenshi.com/catalog/g/gI-06210/ | ほぼ互換品：IR2302ならhttps://akizukidenshi.com/catalog/g/gI-15656/
電流センサ ACS712ELCTR-30A-T | 350 | 1 | 350 | https://akizukidenshi.com/catalog/g/gI-12292/ | 30Aから10Aに変更：https://akizukidenshi.com/catalog/g/gI-14880/
3端子レギュレータ NJM7812SDL1 | 30 | 1 | 30 | https://akizukidenshi.com/catalog/g/gI-10978/
 |  |  | 1672.6

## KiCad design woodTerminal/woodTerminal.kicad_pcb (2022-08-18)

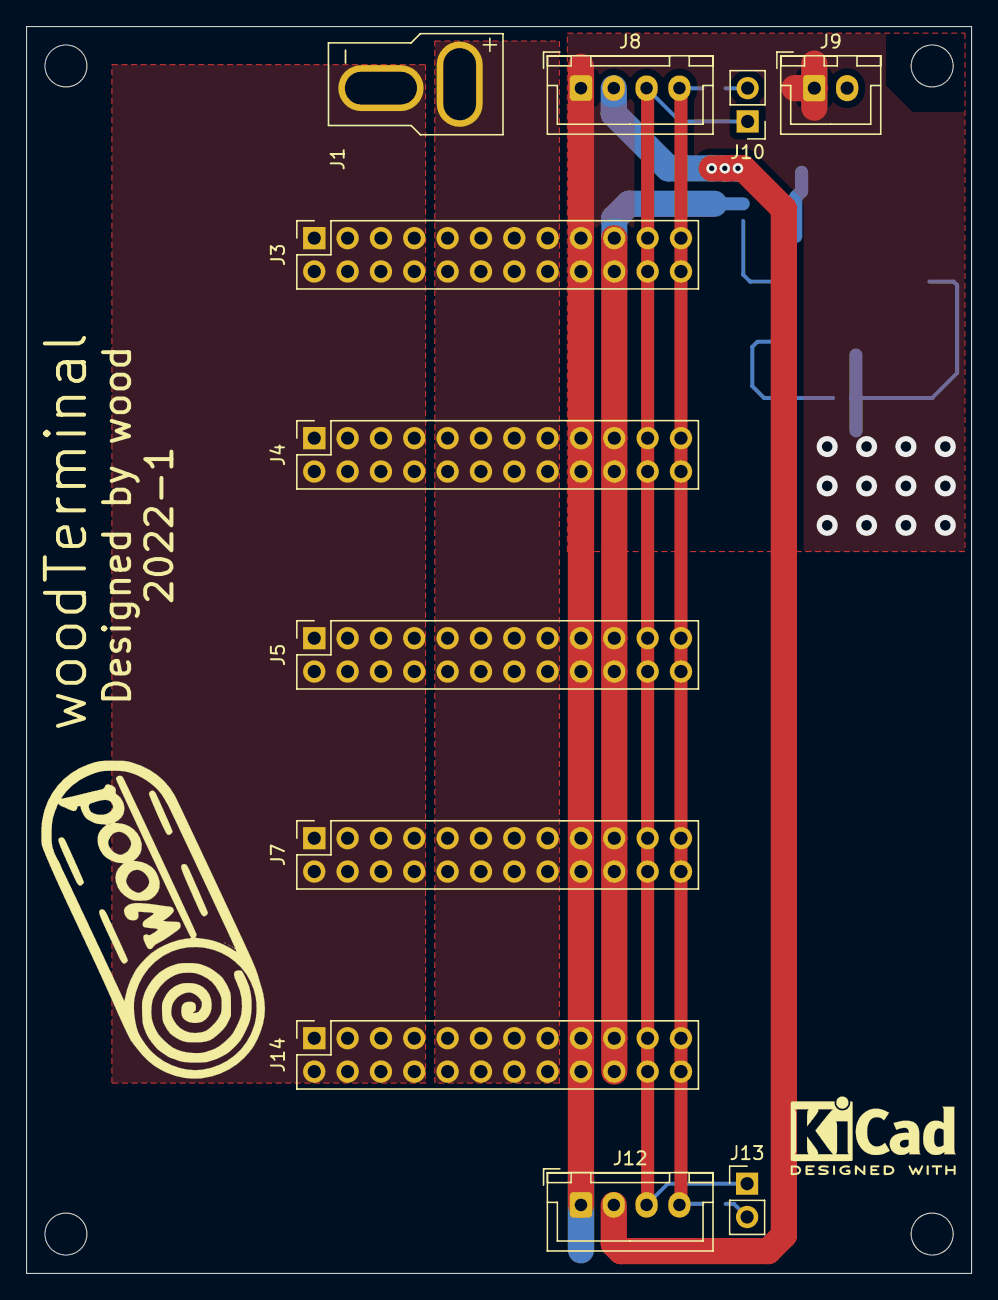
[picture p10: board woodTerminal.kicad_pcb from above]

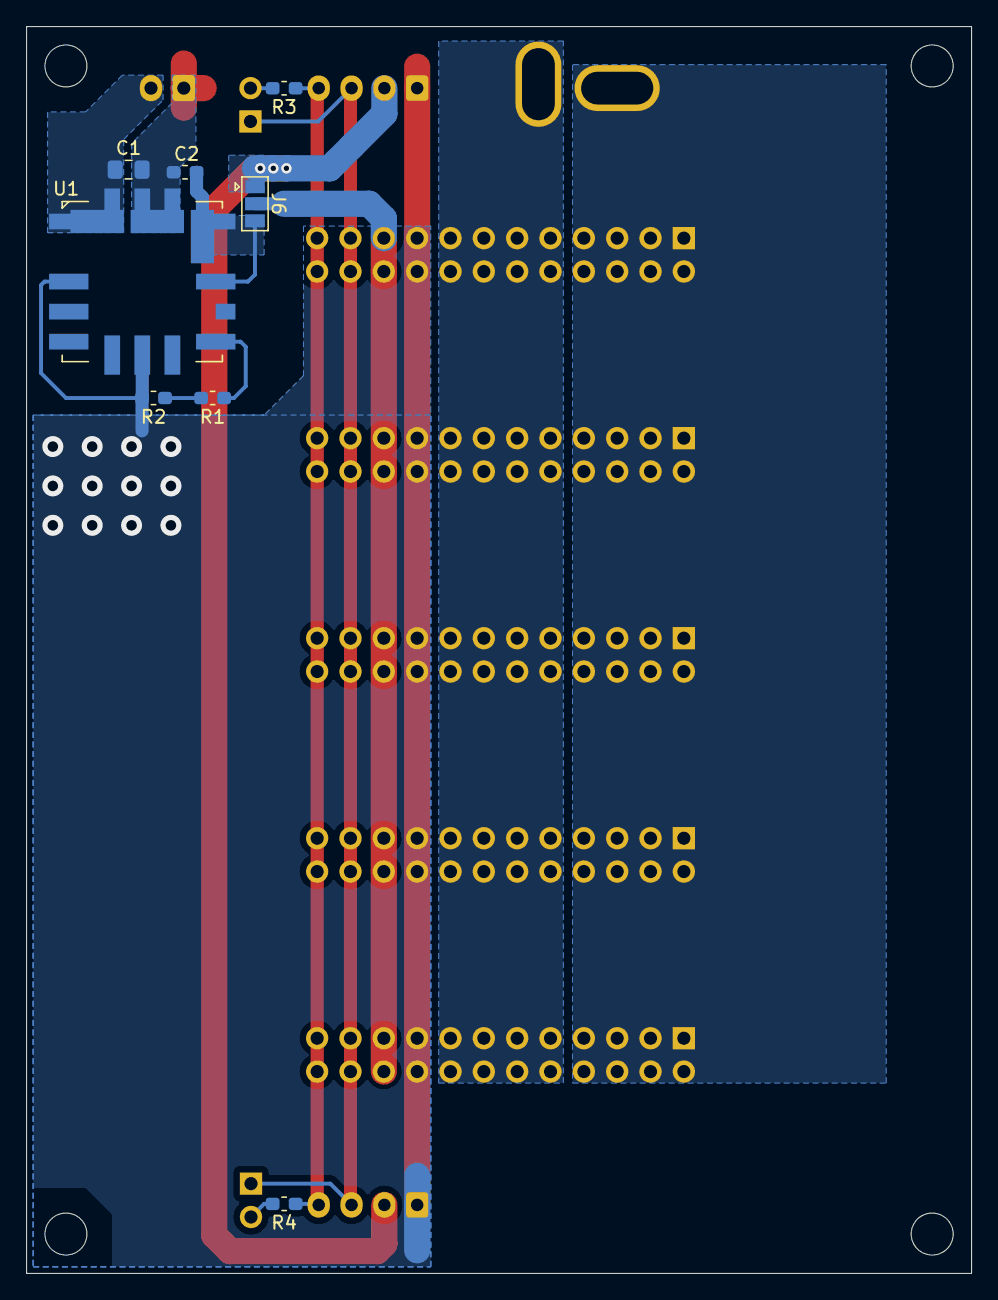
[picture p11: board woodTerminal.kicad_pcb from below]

Board: 2 copper layers, 72.0 x 95.0 mm, 23 parts (8 on the bottom side), 13 nets.

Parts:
 : MountingHole_3.2mm_M3
 #2,  #3,  #4: MountingHole_3.2mm_M3
C1: 22u; C_0805_2012Metric_Pad1.15x1.40mm_HandSolder
C2: 10u; C_0603_1608Metric_Pad1.05x0.95mm_HandSolder
J1: Conn_01x02; DeansTConnector_Male
J3, J4, J5, J7, J14: Conn_02x12_Odd_Even; PinSocket_2x12_P2.54mm_Vertical
J6: Conn_01x03; SolderJumper-3_P1.3mm_Open_Pad1.0x1.5mm
J8, J12: Conn_01x04; JST_XH_B4B-XH-A_1x04_P2.50mm_Vertical
J9: Conn_01x02; JST_XH_B2B-XH-A_1x02_P2.50mm_Vertical
J10, J13: Conn_01x02; PinHeader_1x02_P2.54mm_Vertical
R1: 1k; R_0603_1608Metric_Pad1.05x0.95mm_HandSolder
R2: 330; R_0603_1608Metric_Pad1.05x0.95mm_HandSolder
R3, R4: 120; R_0603_1608Metric_Pad1.05x0.95mm_HandSolder
U1: DCDC_Converter_OKL

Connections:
+5V: J3.19, J3.20, J4.19, J4.20, J5.19, J5.20, J6.2, J7.19, J7.20, J14.19, J14.20
+BATT: J1.2, J3.9, J3.10, J3.11, J3.12, J3.13, J3.14, J3.15, J3.16, J4.9, J4.10, J4.11, J4.12, J4.13, J4.14, J4.15, J4.16, J5.9, J5.10, J5.11, J5.12, J5.13, J5.14, J5.15, J5.16, J7.9, J7.10, J7.11, J7.12, J7.13, J7.14, J7.15, J7.16, J14.9, J14.10, J14.11, J14.12, J14.13, J14.14, J14.15, J14.16
/DCDC_OUT: C2.1, J6.3, U1.4, U1.5
/RS485_5V: J6.1, J8.2, J12.2
/RS485_A: J3.23, J3.24, J4.23, J4.24, J5.23, J5.24, J7.23, J7.24, J8.4, J12.4, J14.23, J14.24, R3.1, R4.1
/RS485_B: J3.21, J3.22, J4.21, J4.22, J5.21, J5.22, J7.21, J7.22, J8.3, J10.1, J12.3, J13.1, J14.21, J14.22
GND: C1.2, C2.2, J3.17, J3.18, J4.17, J4.18, J5.17, J5.18, J7.17, J7.18, J8.1, J9.1, J12.1, J14.17, J14.18, R2.2, U1.1, U1.3, U1.7
GNDPWR: J1.1, J3.1, J3.2, J3.3, J3.4, J3.5, J3.6, J3.7, J3.8, J4.1, J4.2, J4.3, J4.4, J4.5, J4.6, J4.7, J4.8, J5.1, J5.2, J5.3, J5.4, J5.5, J5.6, J5.7, J5.8, J7.1, J7.2, J7.3, J7.4, J7.5, J7.6, J7.7, J7.8, J14.1, J14.2, J14.3, J14.4, J14.5, J14.6, J14.7, J14.8
unnamed: J10.2, R3.2
unnamed: J13.2, R4.2
unnamed: R1.1, U1.6
unnamed: R1.2, R2.1
VCC: C1.1, J9.2, U1.2

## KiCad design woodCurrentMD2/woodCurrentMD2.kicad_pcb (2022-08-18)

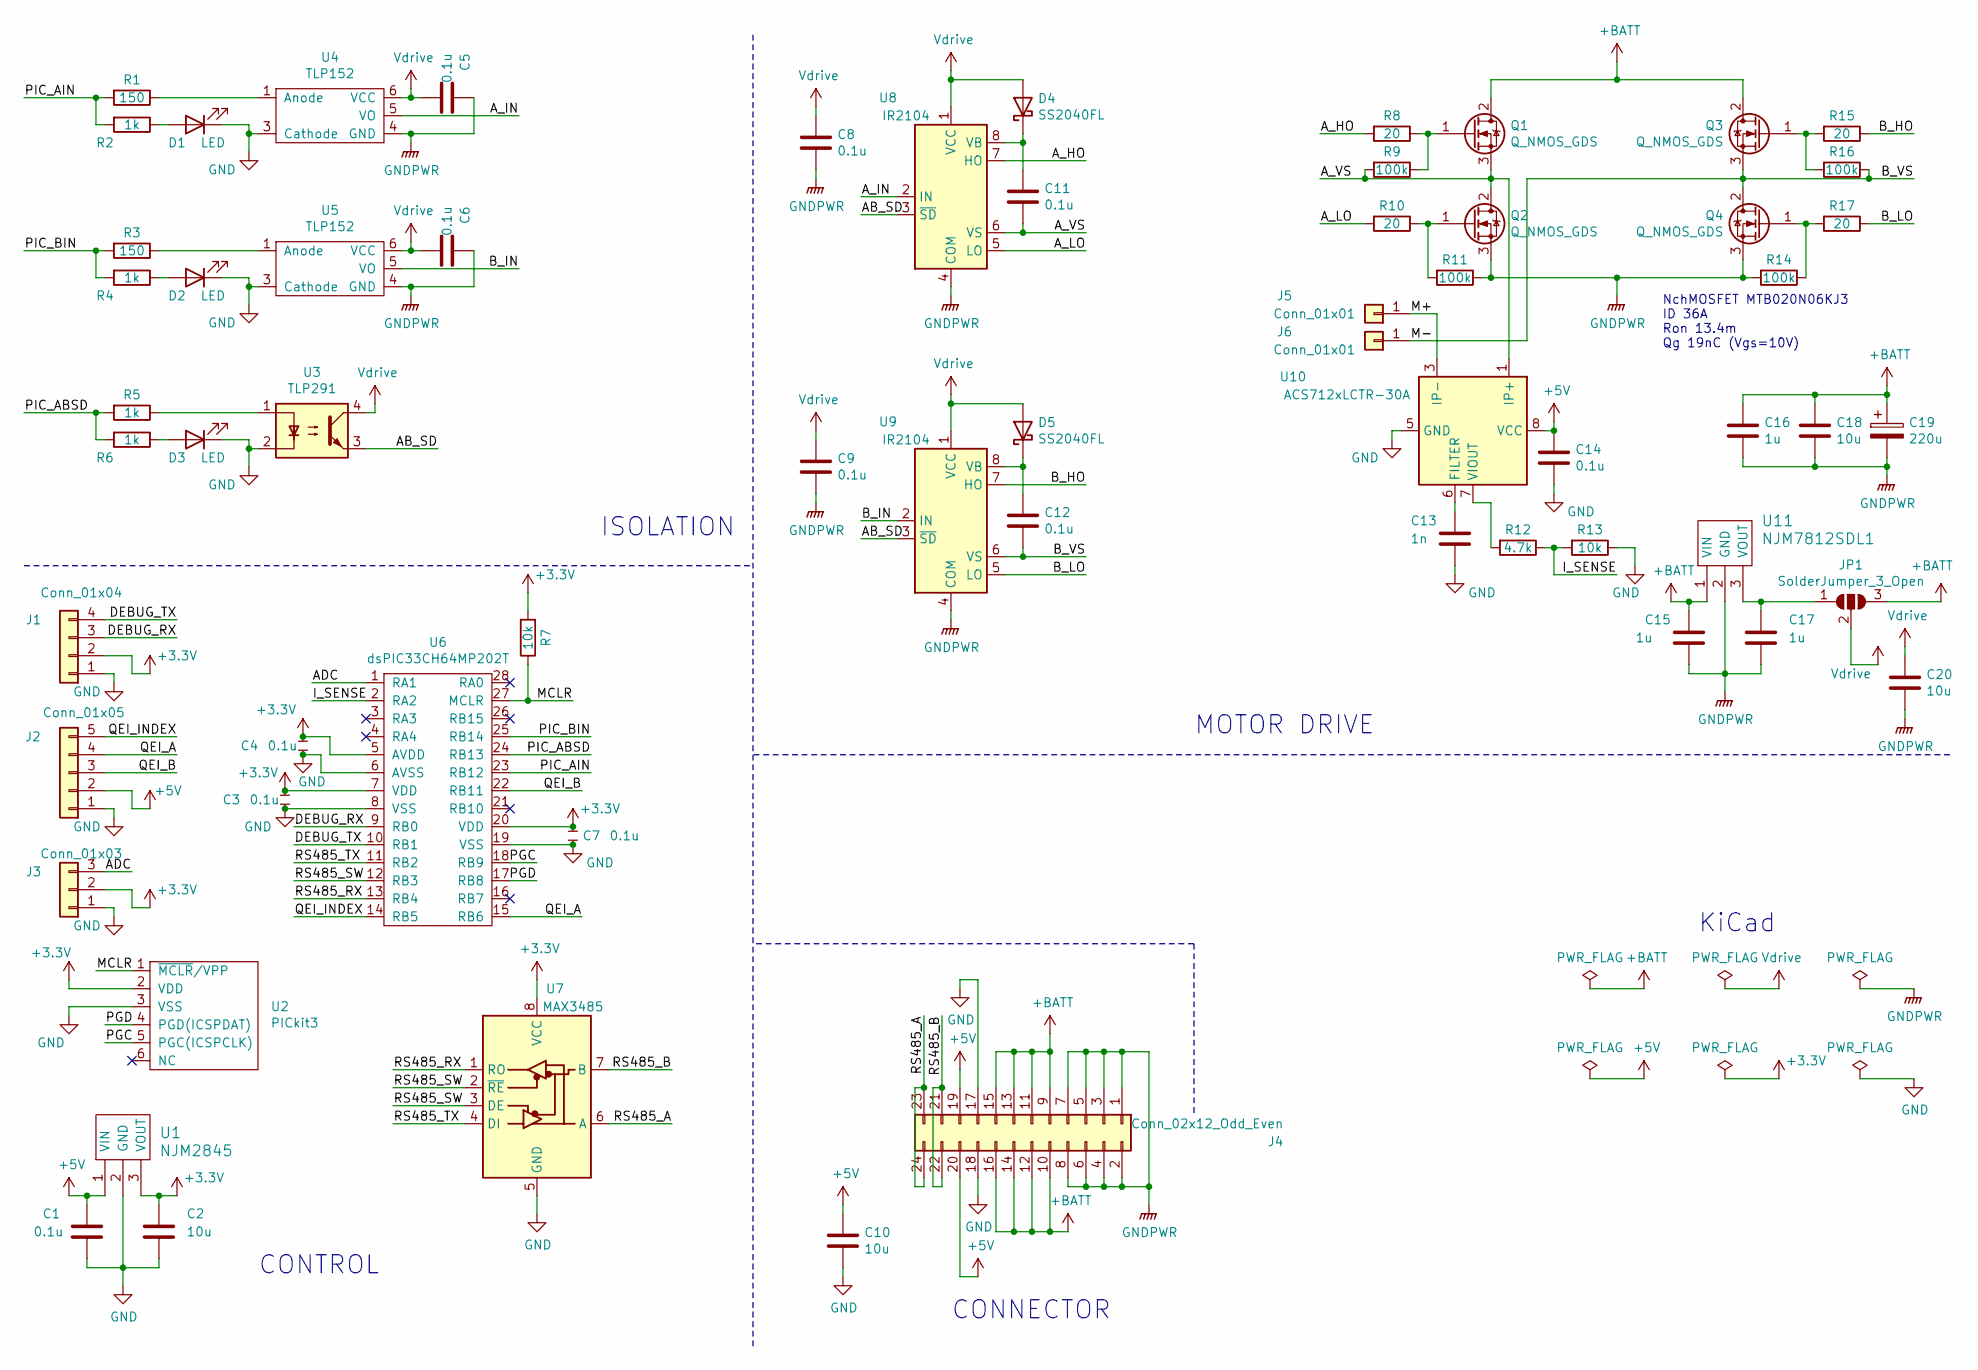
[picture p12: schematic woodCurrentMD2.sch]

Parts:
C1, C3, C4, C5, C6, C7, C8, C9, C11, C12, C14: 0.1u; C_0603_1608Metric
C2, C10, C18, C20: 10u; C_0603_1608Metric
C13: 1n; C_0603_1608Metric
C15, C16, C17: 1u; C_0603_1608Metric
C19: 220u; CP_Elec_10x10
D1, D2, D3: LED; LED_0603_1608Metric
D4, D5: SS2040FL; D_1206_3216Metric
J1: Conn_01x04; JST_XH_S4B-XH-A_1x04_P2.50mm_Horizontal
J2: Conn_01x05; JST_XH_S5B-XH-A_1x05_P2.50mm_Horizontal
J3: Conn_01x03; JST_XH_S3B-XH-A_1x03_P2.50mm_Horizontal
J4: Conn_02x12_Odd_Even; PinHeader_2x12_P2.54mm_Vertical
J5, J6: Conn_01x01; MountingHole_2.2mm_M2_Pad
JP1: SolderJumper_3_Open; SolderJumper-3_P1.3mm_Open_RoundedPad1.0x1.5mm_NumberLabels
Q1, Q2, Q3, Q4: Q_NMOS_GDS; TO-252-2
R1, R3: 150; R_0603_1608Metric
R2, R4, R5, R6: 1k; R_0603_1608Metric
R7, R13: 10k; R_0603_1608Metric
R8, R10, R15, R17: 20; R_0603_1608Metric
R9, R11, R14, R16: 100k; R_0603_1608Metric
R12: 4.7k; R_0603_1608Metric
U1: NJM2845; TO-252-2
U2: PICkit3; PinHeader_1x06_P2.54mm_Horizontal
U3: TLP291; SOIC-4_4.55x2.6mm_P1.27mm
U4, U5: TLP152; SO-6_4.4x3.6mm_P1.27mm
U6: dsPIC33CH64MP202T; SSOP-28_5.3x10.2mm_P0.65mm
U7: MAX3485; SOIC-8_3.9x4.9mm_P1.27mm
U8, U9: IR2104; SOIC-8_3.9x4.9mm_P1.27mm
U10: ACS712xLCTR-30A; SOIC-8_3.9x4.9mm_P1.27mm
U11: NJM7812SDL1; TO-252-2

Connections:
+3V3: C2.1, C3.1, C4.1, C7.1, J1.2, J3.2, R7.2, U1.3 (VOUT), U2.2 (VDD), U6.5 (AVDD), U6.7 (VDD), U6.20 (VDD), U7.8 (VCC)
+5V: C1.1, C10.1, C14.1, J2.2, J4.19, J4.20, U1.1 (VIN), U10.8 (VCC)
+BATT: C15.1, C16.1, C18.1, C19.1, J4.9, J4.10, J4.11, J4.12, J4.13, J4.14, J4.15, J4.16, JP1.3 (B), Q1.2 (D), Q3.2 (D), U11.1 (VIN)
/AB_SD: U3.3, U8.3 (~SD), U9.3 (~SD)
/ADC: J3.3, U6.1 (RA1)
/A_HO: R8.2, U8.7 (HO)
/A_IN: U4.5 (VO), U8.2 (IN)
/A_LO: R10.2, U8.5 (LO)
/A_VS: C11.2, Q1.3 (S), Q2.2 (D), R9.2, U8.6 (VS), U10.1 (IP+), U10.2 (IP+)
/B_HO: R15.1, U9.7 (HO)
/B_IN: U5.5 (VO), U9.2 (IN)
/B_LO: R17.1, U9.5 (LO)
/B_VS: C12.2, J6.1, Q3.3 (S), Q4.2 (D), R16.1, U9.6 (VS)
/DEBUG_RX: J1.3, U6.9 (RB0)
/DEBUG_TX: J1.4, U6.10 (RB1)
/I_SENSE: R12.1, R13.2, U6.2 (RA2)
/M+: J5.1, U10.3 (IP-), U10.4 (IP-)
/MCLR: R7.1, U2.1 (~MCLR~/VPP), U6.27 (MCLR)
/PGC: U2.5 (PGC(ICSPCLK)), U6.18 (RB9)
/PGD: U2.4 (PGD(ICSPDAT)), U6.17 (RB8)
/PIC_ABSD: R5.2, R6.2, U6.24 (RB13)
/PIC_AIN: R1.2, R2.2, U6.23 (RB12)
/PIC_BIN: R3.2, R4.2, U6.25 (RB14)
/QEI_A: J2.4, U6.15 (RB6)
/QEI_B: J2.3, U6.22 (RB11)
/QEI_INDEX: J2.5, U6.14 (RB5)
/RS485_A: J4.23, J4.24, U7.6 (A)
/RS485_B: J4.21, J4.22, U7.7 (B)
/RS485_RX: U6.13 (RB4), U7.1 (RO)
/RS485_SW: U6.12 (RB3), U7.2 (~RE), U7.3 (DE)
/RS485_TX: U6.11 (RB2), U7.4 (DI)
GND: C1.2, C2.2, C3.2, C4.2, C7.2, C10.2, C13.2, C14.2, D1.1 (K), D2.1 (K), D3.1 (K), J1.1, J2.1, J3.1, J4.17, J4.18, R13.1, U1.2 (GND), U2.3 (VSS), U3.2, U4.3 (Cathode), U5.3 (Cathode), U6.6 (AVSS), U6.8 (VSS), U6.19 (VSS), U7.5 (GND), U10.5 (GND)
GNDPWR: C5.1, C6.1, C8.2, C9.2, C15.2, C16.2, C17.2, C18.2, C19.2, C20.2, J4.1, J4.2, J4.3, J4.4, J4.5, J4.6, J4.7, J4.8, Q2.3 (S), Q4.3 (S), R11.1, R14.2, U4.4 (GND), U5.4 (GND), U8.4 (COM), U9.4 (COM), U11.2 (GND)
unnamed: C11.1, D4.1 (K), U8.8 (VB)
unnamed: C12.1, D5.1 (K), U9.8 (VB)
unnamed: C13.1, U10.6 (FILTER)
unnamed: C17.1, JP1.1 (A), U11.3 (VOUT)
unnamed: D1.2 (A), R2.1
unnamed: D2.2 (A), R4.1
unnamed: D3.2 (A), R6.1
unnamed: Q1.1 (G), R8.1, R9.1
unnamed: Q2.1 (G), R10.1, R11.2
unnamed: Q3.1 (G), R15.2, R16.2
unnamed: Q4.1 (G), R14.1, R17.2
unnamed: R1.1, U4.1 (Anode)
unnamed: R3.1, U5.1 (Anode)
unnamed: R5.1, U3.1
unnamed: R12.2, U10.7 (VIOUT)
Vdrive: C5.2, C6.2, C8.1, C9.1, C20.1, D4.2 (A), D5.2 (A), JP1.2 (C), U3.4, U4.6 (VCC), U5.6 (VCC), U8.1 (VCC), U9.1 (VCC)

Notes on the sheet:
CONTROL
ISOLATION
CONNECTOR
KiCad
MOTOR DRIVE
NchMOSFET MTB020N06KJ3 ID 36A Ron 13.4m Qg 19nC (Vgs=10V)

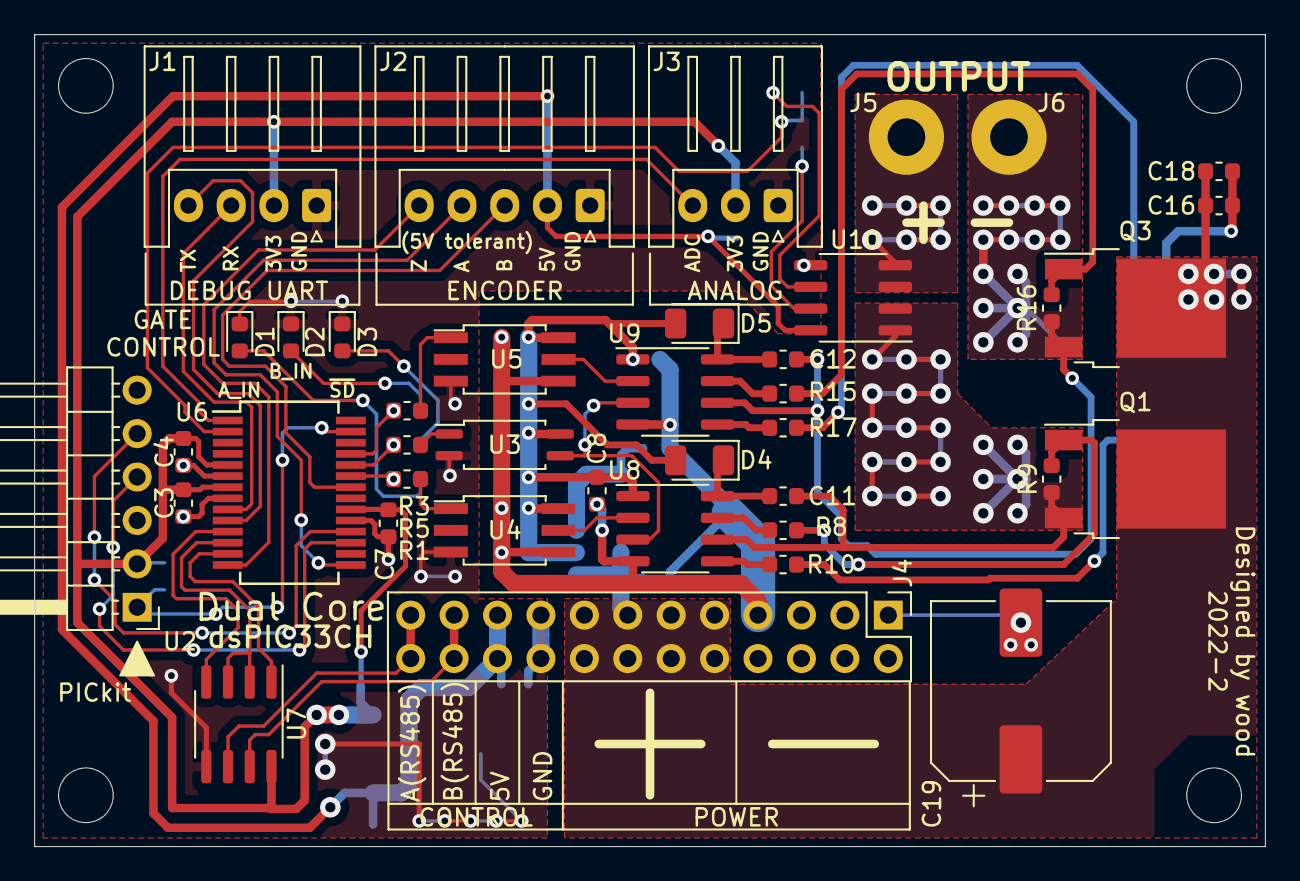
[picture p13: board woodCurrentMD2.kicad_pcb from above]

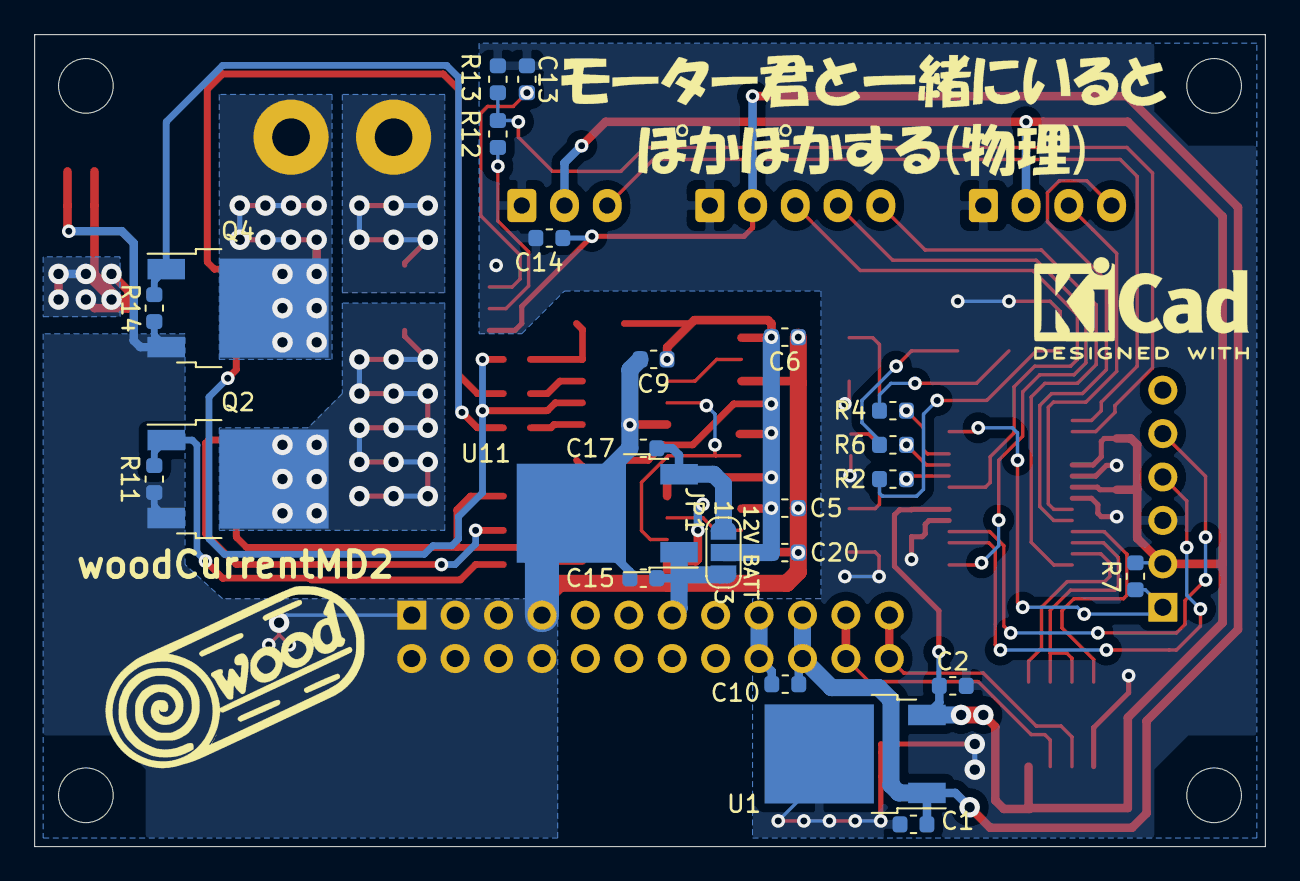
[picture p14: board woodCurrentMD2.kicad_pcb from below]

Board: 2 copper layers, 72.0 x 47.5 mm, 68 parts (24 on the bottom side), 49 nets.

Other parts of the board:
 : MountingHole_3.2mm_M3
 #2,  #3,  #4: MountingHole_3.2mm_M3

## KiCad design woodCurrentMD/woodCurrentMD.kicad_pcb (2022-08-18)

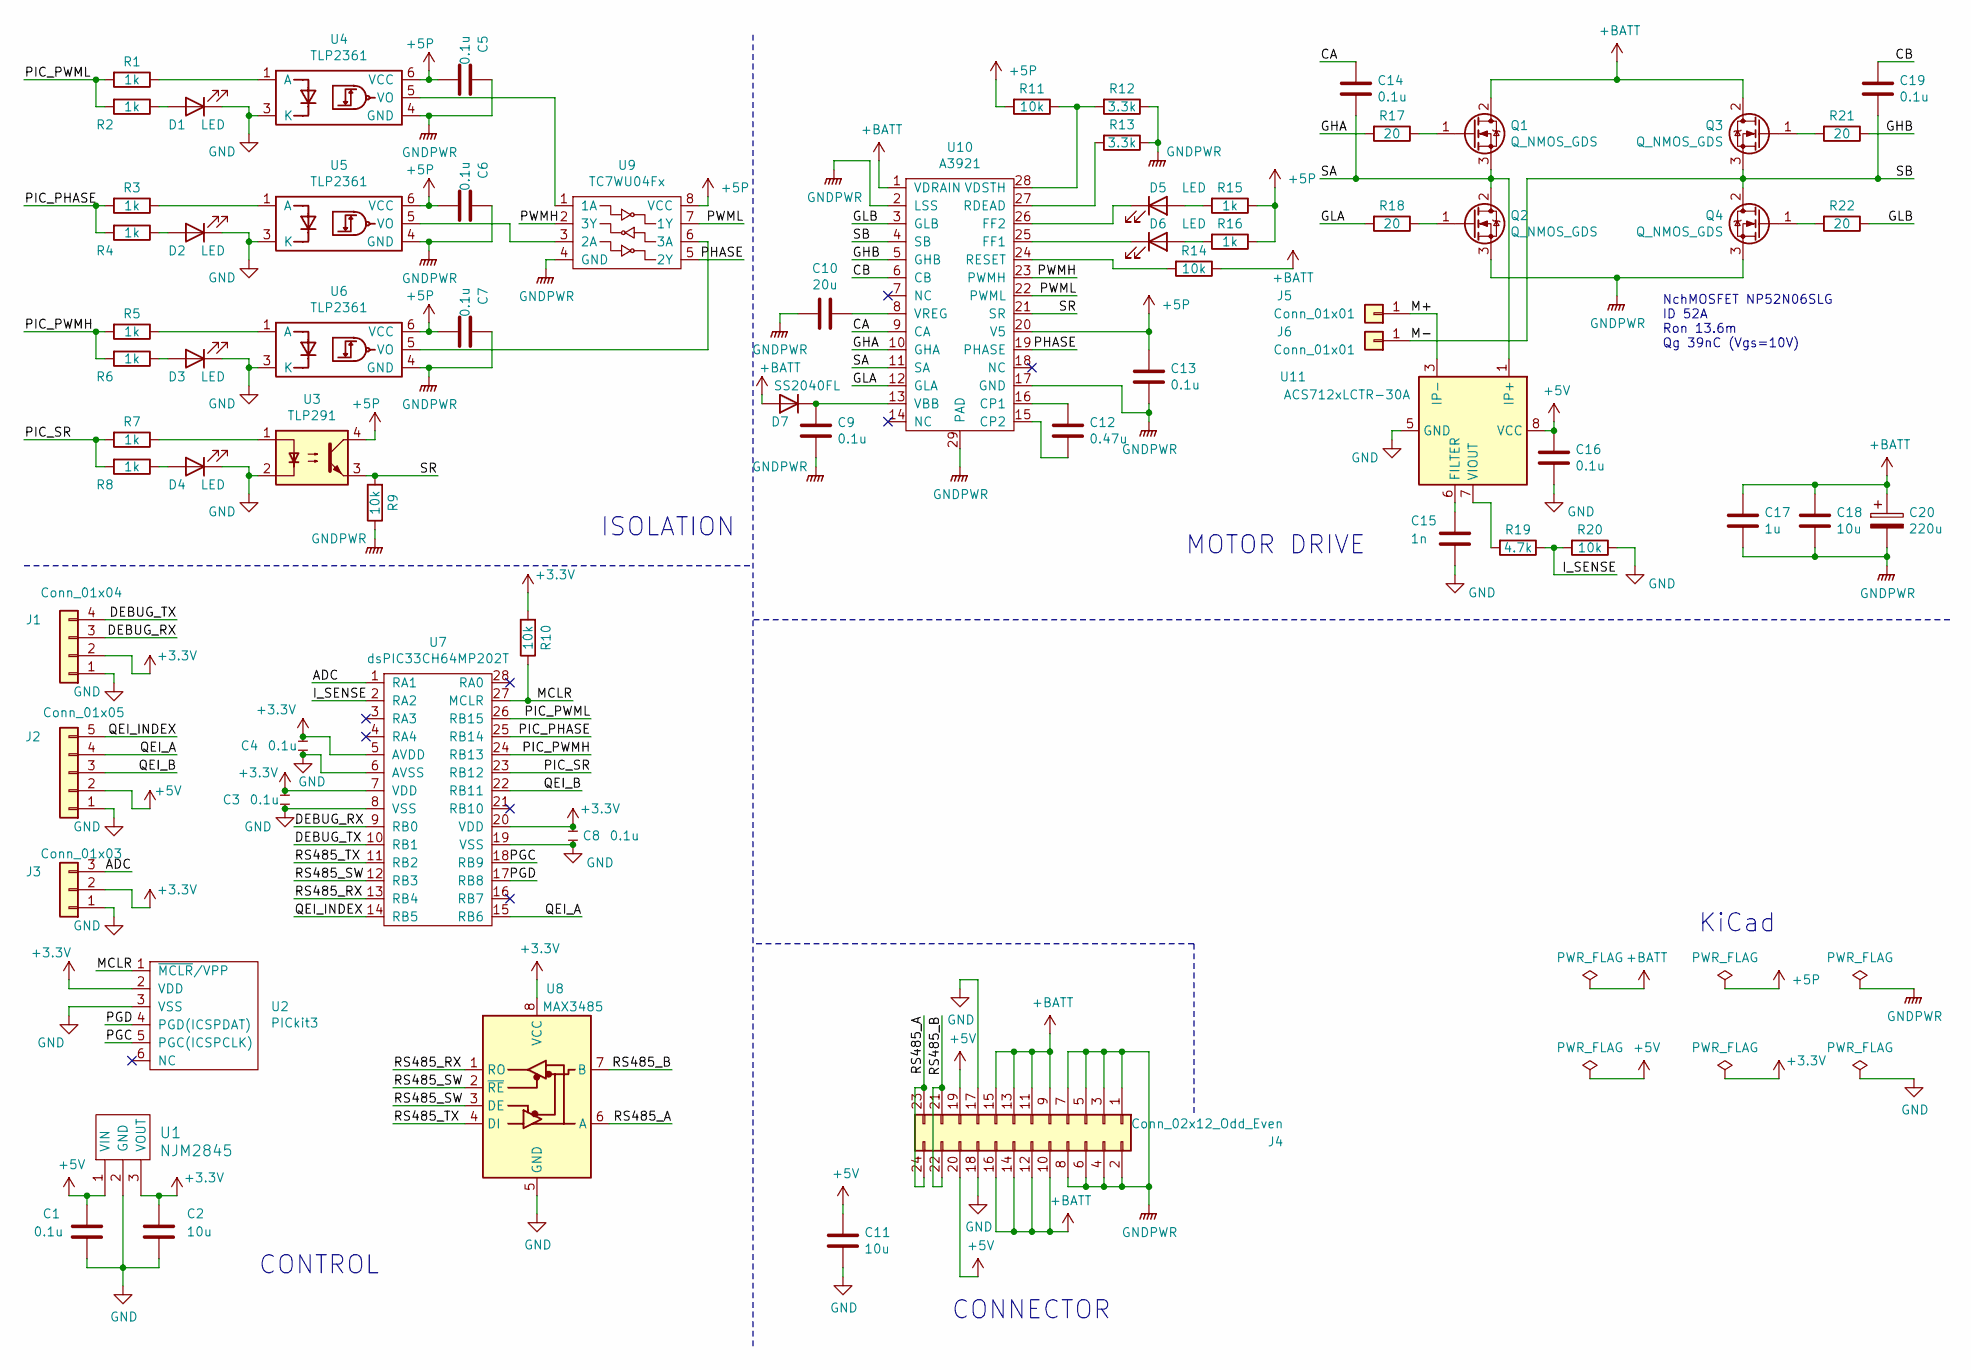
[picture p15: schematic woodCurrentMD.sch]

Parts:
C1, C3, C4, C5, C6, C7, C8, C9, C13, C14, C16, C19: 0.1u; C_0603_1608Metric
C2, C11, C18: 10u; C_0603_1608Metric
C10: 20u; C_0805_2012Metric
C12: 0.47u; C_0603_1608Metric
C15: 1n; C_0603_1608Metric
C17: 1u; C_0603_1608Metric
C20: 220u; CP_Elec_10x10
D1, D2, D3, D4, D5, D6: LED; LED_0603_1608Metric
D7: SS2040FL; D_1206_3216Metric
J1: Conn_01x04; JST_XH_S4B-XH-A_1x04_P2.50mm_Horizontal
J2: Conn_01x05; JST_XH_S5B-XH-A_1x05_P2.50mm_Horizontal
J3: Conn_01x03; JST_XH_S3B-XH-A_1x03_P2.50mm_Horizontal
J4: Conn_02x12_Odd_Even; PinHeader_2x12_P2.54mm_Vertical
J5, J6: Conn_01x01; MountingHole_2.2mm_M2_Pad
Q1, Q2, Q3, Q4: Q_NMOS_GDS; TO-252-2
R1, R2, R3, R4, R5, R6, R7, R8, R15, R16: 1k; R_0603_1608Metric
R9, R10, R11, R14, R20: 10k; R_0603_1608Metric
R12, R13: 3.3k; R_0603_1608Metric
R17, R18, R21, R22: 20; R_0603_1608Metric
R19: 4.7k; R_0603_1608Metric
U1: NJM2845; TO-252-2
U2: PICkit3; PinHeader_1x06_P2.54mm_Horizontal
U3: TLP291; SOIC-4_4.55x2.6mm_P1.27mm
U4, U5, U6: TLP2361; SO-6_4.4x3.6mm_P1.27mm
U7: dsPIC33CH64MP202T; SSOP-28_5.3x10.2mm_P0.65mm
U8: MAX3485; SOIC-8_3.9x4.9mm_P1.27mm
U9: TC7WU04Fx; SSOP-8_2.95x2.8mm_P0.65mm
U10: A3921; HTSSOP-28-1EP_4.4x9.7mm_P0.65mm_EP2.85x5.4mm
U11: ACS712xLCTR-30A; SOIC-8_3.9x4.9mm_P1.27mm

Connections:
+3V3: C2.1, C3.1, C4.1, C8.1, J1.2, J3.2, R10.2, U1.3 (VOUT), U2.2 (VDD), U7.5 (AVDD), U7.7 (VDD), U7.20 (VDD), U8.8 (VCC)
+5P: C5.2, C6.2, C7.2, C13.1, R11.2, R15.1, R16.1, U3.4, U4.6 (VCC), U5.6 (VCC), U6.6 (VCC), U9.8 (VCC), U10.20 (V5)
+5V: C1.1, C11.1, C16.1, J2.2, J4.19, J4.20, U1.1 (VIN), U11.8 (VCC)
+BATT: C17.1, C18.1, C20.1, D7.2 (A), J4.9, J4.10, J4.11, J4.12, J4.13, J4.14, J4.15, J4.16, Q1.2 (D), Q3.2 (D), R14.1, U10.1 (VDRAIN)
/ADC: J3.3, U7.1 (RA1)
/CA: C14.1, U10.9 (CA)
/CB: C19.1, U10.6 (CB)
/DEBUG_RX: J1.3, U7.9 (RB0)
/DEBUG_TX: J1.4, U7.10 (RB1)
/GHA: R17.2, U10.10 (GHA)
/GHB: R21.1, U10.5 (GHB)
/GLA: R18.2, U10.12 (GLA)
/GLB: R22.1, U10.3 (GLB)
/I_SENSE: R19.1, R20.2, U7.2 (RA2)
/M+: J5.1, U11.3 (IP-), U11.4 (IP-)
/M-: C19.2, J6.1, Q3.3 (S), Q4.2 (D), U10.4 (SB)
/MCLR: R10.1, U2.1 (~MCLR~/VPP), U7.27 (MCLR)
/PGC: U2.5 (PGC(ICSPCLK)), U7.18 (RB9)
/PGD: U2.4 (PGD(ICSPDAT)), U7.17 (RB8)
/PHASE: U9.5 (2Y), U10.19 (PHASE)
/PIC_PHASE: R3.2, R4.2, U7.25 (RB14)
/PIC_PWMH: R5.2, R6.2, U7.24 (RB13)
/PIC_PWML: R1.2, R2.2, U7.26 (RB15)
/PIC_SR: R7.2, R8.2, U7.23 (RB12)
/PWMH: U9.2 (3Y), U10.23 (PWMH)
/PWML: U9.7 (1Y), U10.22 (PWML)
/QEI_A: J2.4, U7.15 (RB6)
/QEI_B: J2.3, U7.22 (RB11)
/QEI_INDEX: J2.5, U7.14 (RB5)
/RS485_A: J4.23, J4.24, U8.6 (A)
/RS485_B: J4.21, J4.22, U8.7 (B)
/RS485_RX: U7.13 (RB4), U8.1 (RO)
/RS485_SW: U7.12 (RB3), U8.2 (~RE), U8.3 (DE)
/RS485_TX: U7.11 (RB2), U8.4 (DI)
/SA: C14.2, Q1.3 (S), Q2.2 (D), U10.11 (SA), U11.1 (IP+), U11.2 (IP+)
/SR: R9.2, U3.3, U10.21 (SR)
GND: C1.2, C2.2, C3.2, C4.2, C8.2, C11.2, C15.2, C16.2, D1.1 (K), D2.1 (K), D3.1 (K), D4.1 (K), J1.1, J2.1, J3.1, J4.17, J4.18, R20.1, U1.2 (GND), U2.3 (VSS), U3.2, U4.3 (K), U5.3 (K), U6.3 (K), U7.6 (AVSS), U7.8 (VSS), U7.19 (VSS), U8.5 (GND), U11.5 (GND)
GNDPWR: C5.1, C6.1, C7.1, C9.2, C10.2, C13.2, C17.2, C18.2, C20.2, J4.1, J4.2, J4.3, J4.4, J4.5, J4.6, J4.7, J4.8, Q2.3 (S), Q4.3 (S), R9.1, R12.1, R13.1, U4.4 (GND), U5.4 (GND), U6.4 (GND), U9.4 (GND), U10.2 (LSS), U10.17 (GND), U10.29 (PAD)
unnamed: C9.1, D7.1 (K), U10.13 (VBB)
unnamed: C10.1, U10.8 (VREG)
unnamed: C12.1, U10.16 (CP1)
unnamed: C12.2, U10.15 (CP2)
unnamed: C15.1, U11.6 (FILTER)
unnamed: D1.2 (A), R2.1
unnamed: D2.2 (A), R4.1
unnamed: D3.2 (A), R6.1
unnamed: D4.2 (A), R8.1
unnamed: D5.1 (K), U10.26 (FF2)
unnamed: D5.2 (A), R15.2
unnamed: D6.1 (K), U10.25 (FF1)
unnamed: D6.2 (A), R16.2
unnamed: Q1.1 (G), R17.1
unnamed: Q2.1 (G), R18.1
unnamed: Q3.1 (G), R21.2
unnamed: Q4.1 (G), R22.2
unnamed: R1.1, U4.1 (A)
unnamed: R3.1, U5.1 (A)
unnamed: R5.1, U6.1 (A)
unnamed: R7.1, U3.1
unnamed: R11.1, R12.2, U10.28 (VDSTH)
unnamed: R13.2, U10.27 (RDEAD)
unnamed: R14.2, U10.24 (RESET)
unnamed: R19.2, U11.7 (VIOUT)
unnamed: U4.5 (VO), U9.1 (1A)
unnamed: U5.5 (VO), U9.3 (2A)
unnamed: U6.5 (VO), U9.6 (3A)

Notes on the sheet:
NchMOSFET NP52N06SLG ID 52A Ron 13.6m Qg 39nC (Vgs=10V)
CONTROL
ISOLATION
CONNECTOR
KiCad
MOTOR DRIVE

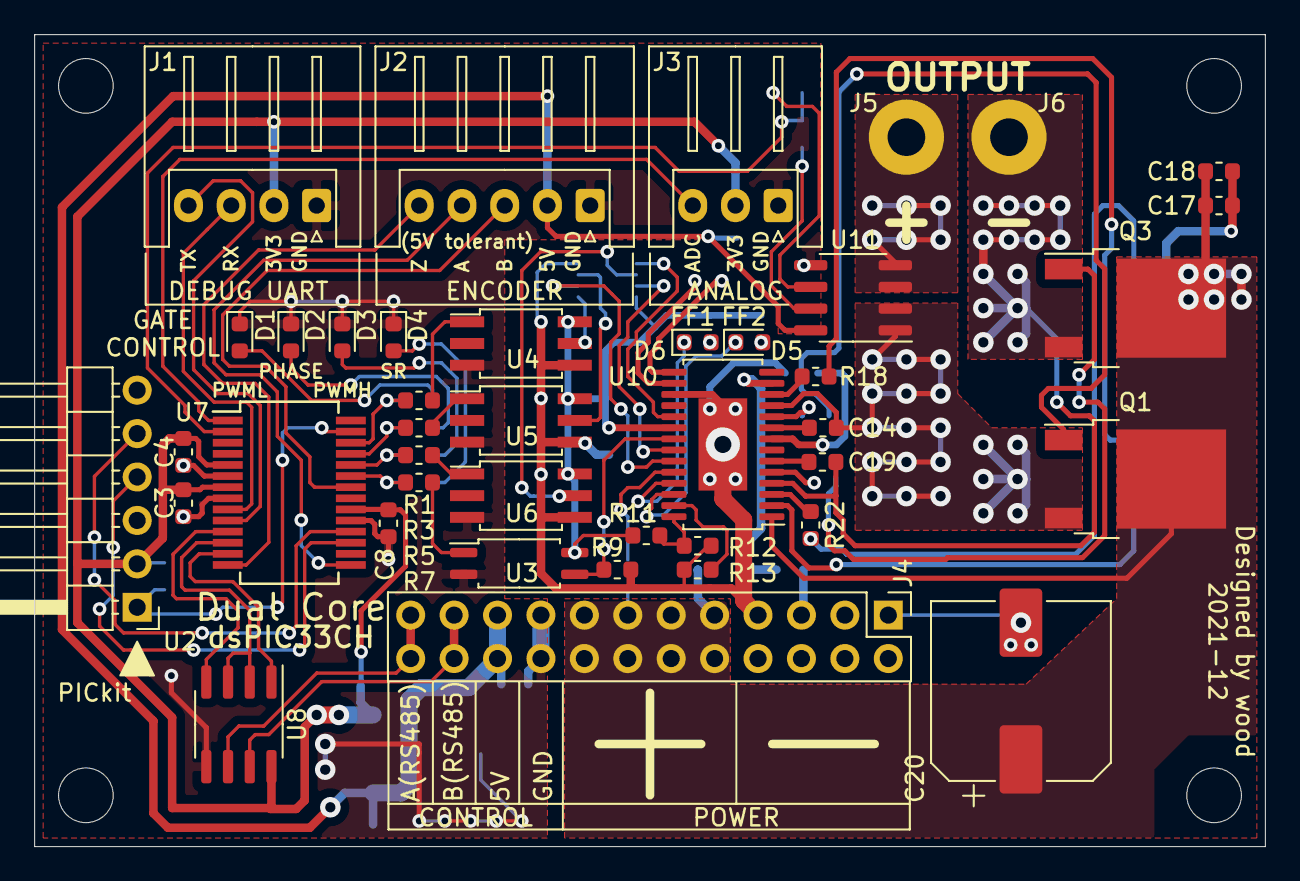
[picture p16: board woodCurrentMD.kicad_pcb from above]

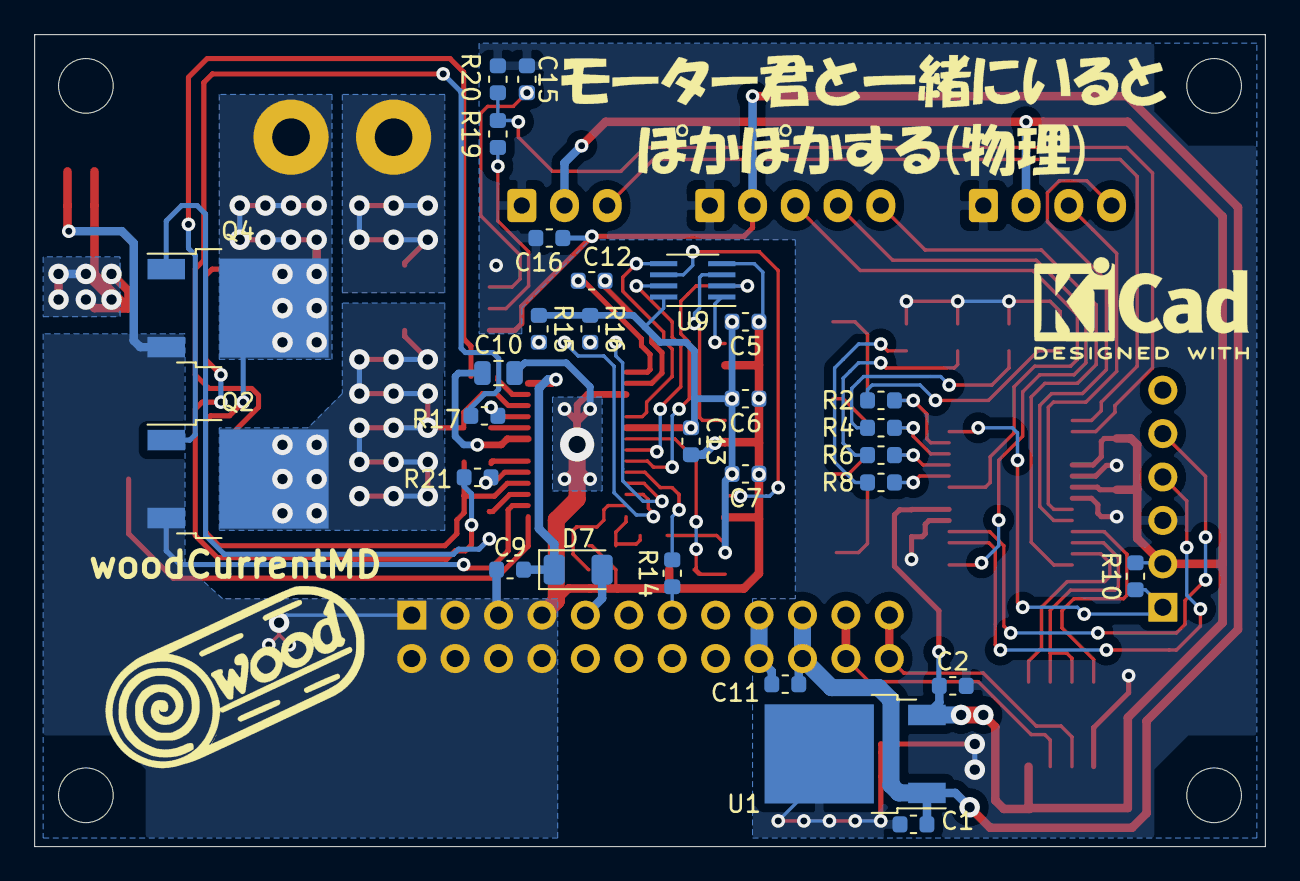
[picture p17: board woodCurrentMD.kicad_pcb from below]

Board: 2 copper layers, 72.0 x 47.5 mm, 74 parts (29 on the bottom side), 66 nets.

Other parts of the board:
 : MountingHole_3.2mm_M3
 #2,  #3,  #4: MountingHole_3.2mm_M3

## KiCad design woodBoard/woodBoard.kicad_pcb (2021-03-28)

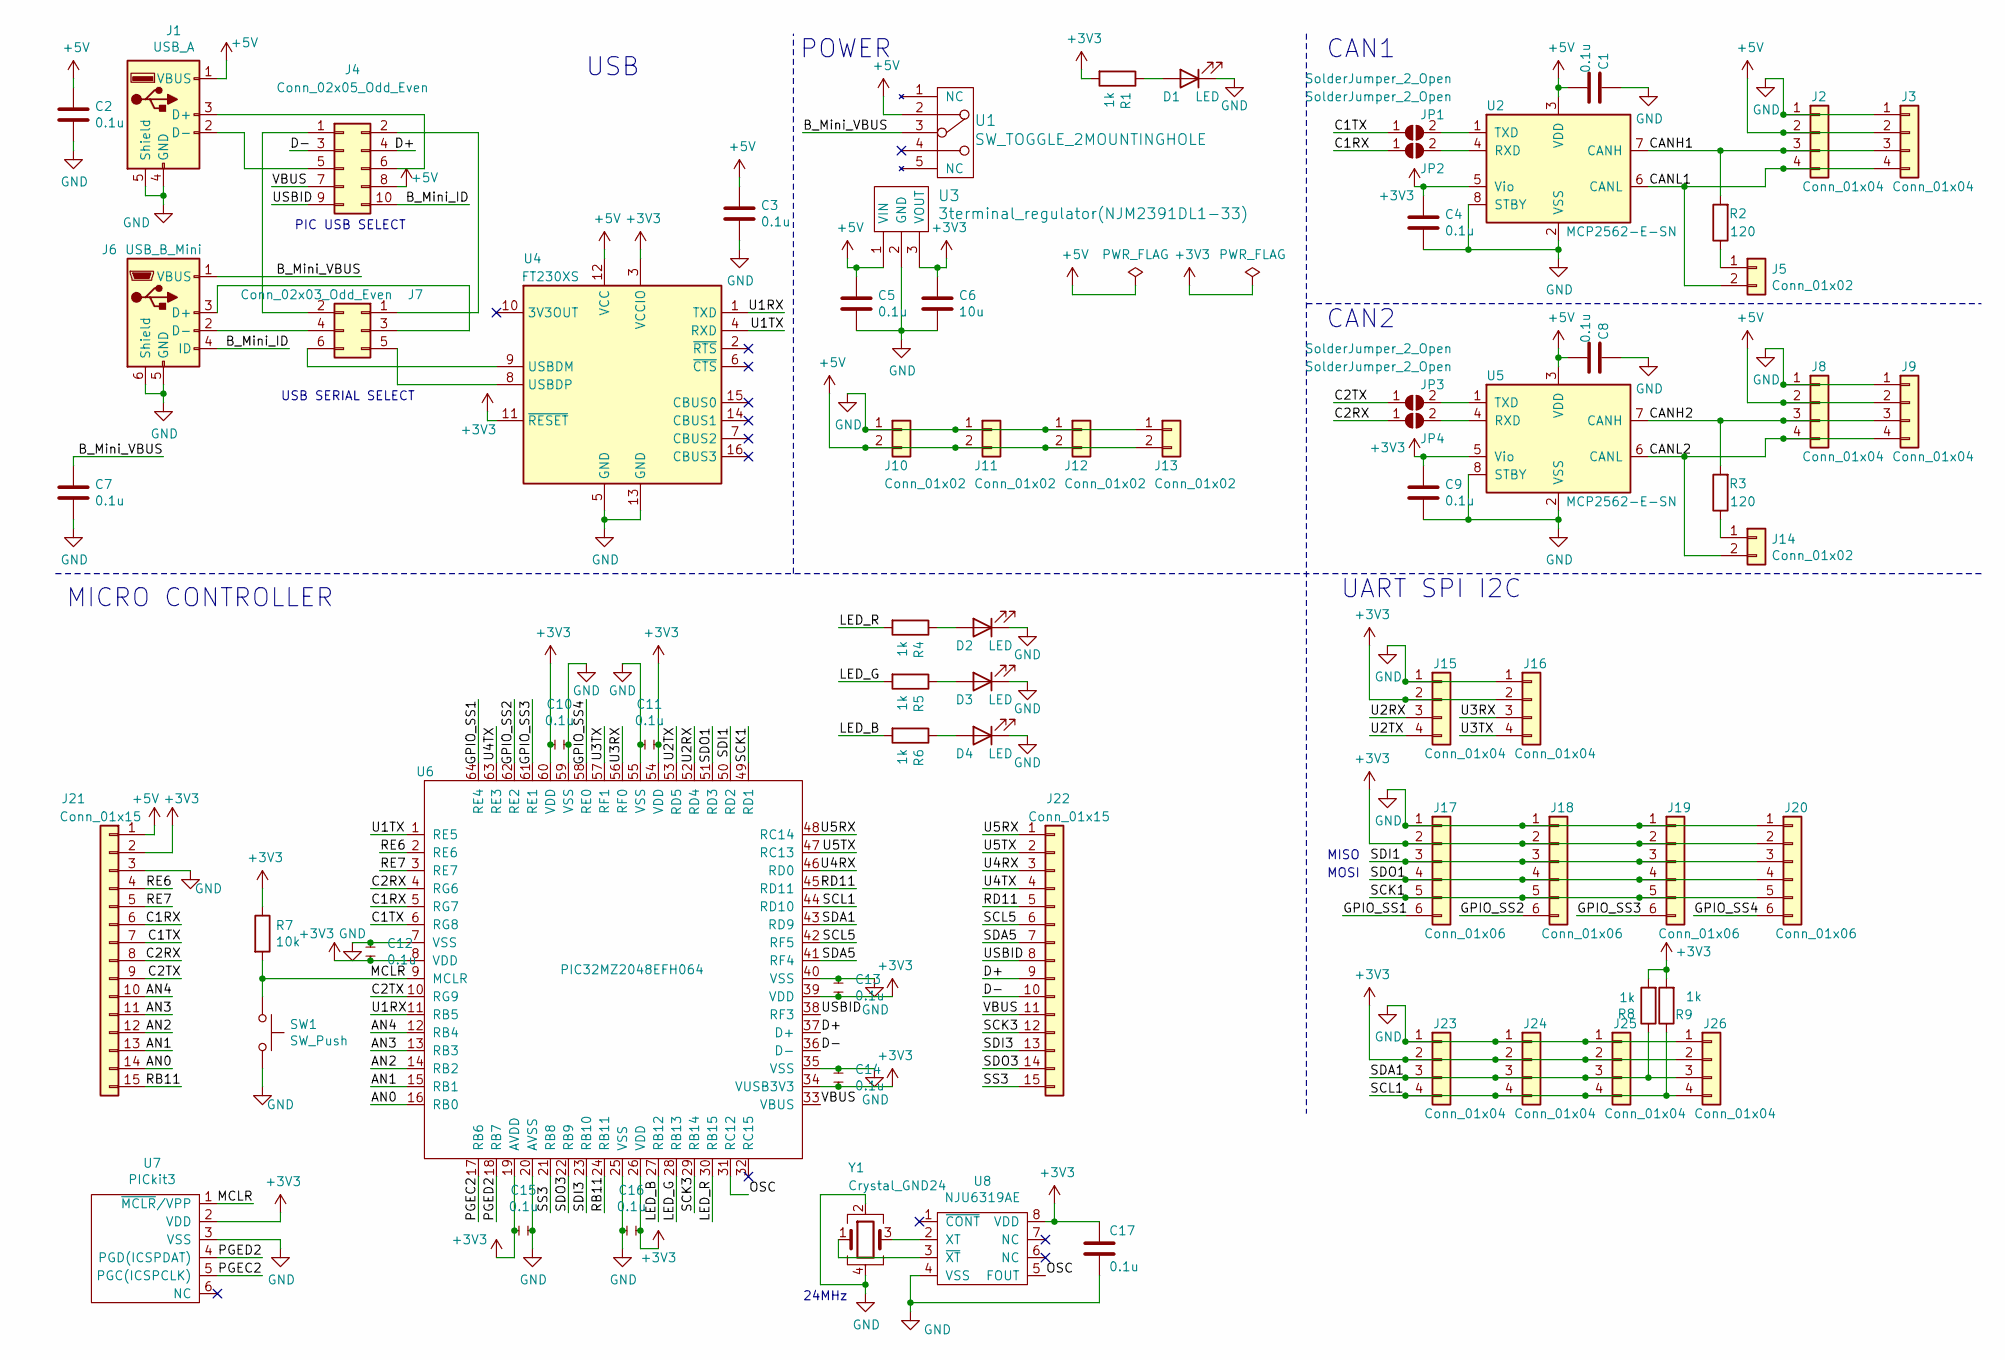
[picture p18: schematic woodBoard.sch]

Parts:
C1, C2, C3, C4, C5, C7, C8, C9, C10, C11, C12, C13, C14, C15, C16, C17: 0.1u; C_0603_1608Metric
C6: 10u; C_0603_1608Metric_Pad1.05x0.95mm_HandSolder
D1, D2, D3, D4: LED; LED_0603_1608Metric_Pad1.05x0.95mm_HandSolder
J1: USB_A; USB_A_Stewart_SS-52100-001_Horizontal
J2, J3, J8, J9, J15, J16, J23, J24, J25, J26: Conn_01x04; JST_EH_B4B-EH-A_1x04_P2.50mm_Vertical
J4: Conn_02x05_Odd_Even; PinHeader_2x05_P2.54mm_Vertical
J5, J14: Conn_01x02; PinHeader_1x02_P2.54mm_Vertical
J6: USB_B_Mini; USB_Mini-B_Wuerth_65100516121_Horizontal
J7: Conn_02x03_Odd_Even; PinHeader_2x03_P2.54mm_Vertical
J10, J11, J12, J13: Conn_01x02; JST_EH_B2B-EH-A_1x02_P2.50mm_Vertical
J17, J18, J19, J20: Conn_01x06; JST_EH_B6B-EH-A_1x06_P2.50mm_Vertical
J21, J22: Conn_01x15; PinSocket_1x15_P2.54mm_Vertical
JP1, JP2, JP3, JP4: SolderJumper_2_Open; SolderJumper-2_P1.3mm_Open_RoundedPad1.0x1.5mm
R1, R4, R5, R6, R8, R9: 1k; R_0603_1608Metric_Pad1.05x0.95mm_HandSolder
R2, R3: 120; R_0603_1608Metric_Pad1.05x0.95mm_HandSolder
R7: 10k; R_0603_1608Metric_Pad1.05x0.95mm_HandSolder
SW1: SW_Push; SW_TVAF06-A020B-R
U1: SW_TOGGLE_2MOUNTINGHOLE; SW_2MS1T1B4VS2QES
U2, U5: MCP2562-E-SN; SOIC-8_3.9x4.9mm_P1.27mm
U3: 3terminal_regulator(NJM2391DL1-33); TO-252-2
U4: FT230XS; QSOP-16_3.9x4.9mm_P0.635mm
U6: PIC32MZ2048EFH064; TQFP-64_10x10mm_P0.5mm
U7: PICkit3; PinHeader_1x06_P2.54mm_Vertical
U8: NJU6319AE; SO-8_3.9x4.9mm_P1.27mm
Y1: Crystal_GND24; Crystal_SMD_SeikoEpson_FA238V-4Pin_3.2x2.5mm_HandSoldering

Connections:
+3V3: C4.1, C6.1, C9.1, C10.1, C11.2, C12.2, C13.2, C14.2, C15.1, C16.2, C17.1, J15.2, J16.2, J17.2, J18.2, J19.2, J20.2, J21.2, J23.2, J24.2, J25.2, J26.2, R1.2, R7.1, R8.2, R9.2, U2.5 (Vio), U3.3 (VOUT), U4.3 (VCCIO), U4.11 (~RESET), U5.5 (Vio), U6.8 (VDD), U6.19 (AVDD), U6.26 (VDD), U6.34 (VUSB3V3), U6.39 (VDD), U6.54 (VDD), U6.60 (VDD), U7.2 (VDD), U8.8 (VDD)
+5V: C1.2, C2.1, C3.1, C5.1, C8.2, J1.1 (VBUS), J2.2, J3.2, J4.8, J8.2, J9.2, J10.2, J11.2, J12.2, J13.2, J21.1, U1.2, U2.3 (VDD), U3.1 (VIN), U4.12 (VCC), U5.3 (VDD)
/AN0: J21.14, U6.16 (RB0)
/AN1: J21.13, U6.15 (RB1)
/AN2: J21.12, U6.14 (RB2)
/AN3: J21.11, U6.13 (RB3)
/AN4: J21.10, U6.12 (RB4)
/B_Mini_ID: J4.10, J6.4 (ID)
/B_Mini_VBUS: C7.1, J6.1 (VBUS), U1.3
/C1RX: J21.6, JP2.1 (A), U6.5 (RG7)
/C1TX: J21.7, JP1.1 (A), U6.6 (RG8)
/C2RX: J21.8, JP4.1 (A), U6.4 (RG6)
/C2TX: J21.9, JP3.1 (A), U6.10 (RG9)
/CANH1: J2.3, J3.3, R2.2, U2.7 (CANH)
/CANH2: J8.3, J9.3, R3.2, U5.7 (CANH)
/CANL1: J2.4, J3.4, J5.2, U2.6 (CANL)
/CANL2: J8.4, J9.4, J14.2, U5.6 (CANL)
/D+: J4.4, J22.9, U6.37 (D+)
/D-: J4.3, J22.10, U6.36 (D-)
/GPIO_SS1: J17.6, U6.64 (RE4)
/GPIO_SS2: J18.6, U6.62 (RE2)
/GPIO_SS3: J19.6, U6.61 (RE1)
/GPIO_SS4: J20.6, U6.58 (RE0)
/LED_B: R6.2, U6.27 (RB12)
/LED_G: R5.2, U6.28 (RB13)
/LED_R: R4.2, U6.30 (RB15)
/MCLR: R7.2, SW1.1, U6.9 (MCLR), U7.1 (~MCLR~/VPP)
/OSC: U6.31 (RC12), U8.5 (FOUT)
/PGEC2: U6.17 (RB6), U7.5 (PGC(ICSPCLK))
/PGED2: U6.18 (RB7), U7.4 (PGD(ICSPDAT))
/RB11: J21.15, U6.24 (RB11)
/RD11: J22.5, U6.45 (RD11)
/RE6: J21.4, U6.2 (RE6)
/RE7: J21.5, U6.3 (RE7)
/SCK1: J17.5, J18.5, J19.5, J20.5, U6.49 (RD1)
/SCK3: J22.12, U6.29 (RB14)
/SCL1: J23.4, J24.4, J25.4, J26.4, R9.1, U6.44 (RD10)
/SCL5: J22.6, U6.42 (RF5)
/SDA1: J23.3, J24.3, J25.3, J26.3, R8.1, U6.43 (RD9)
/SDA5: J22.7, U6.41 (RF4)
/SDI1: J17.3, J18.3, J19.3, J20.3, U6.50 (RD2)
/SDI3: J22.13, U6.23 (RB10)
/SDO1: J17.4, J18.4, J19.4, J20.4, U6.51 (RD3)
/SDO3: J22.14, U6.22 (RB9)
/SS3: J22.15, U6.21 (RB8)
/U1RX: U4.1 (TXD), U6.11 (RB5)
/U1TX: U4.4 (RXD), U6.1 (RE5)
/U2RX: J15.3, U6.52 (RD4)
/U2TX: J15.4, U6.53 (RD5)
/U3RX: J16.3, U6.56 (RF0)
/U3TX: J16.4, U6.57 (RF1)
/U4RX: J22.3, U6.46 (RD0)
/U4TX: J22.4, U6.63 (RE3)
/U5RX: J22.1, U6.48 (RC14)
/U5TX: J22.2, U6.47 (RC13)
/USBID: J4.9, J22.8, U6.38 (RF3)
/VBUS: J4.7, J22.11, U6.33 (VBUS)
GND: C1.1, C2.2, C3.2, C4.2, C5.2, C6.2, C7.2, C8.1, C9.2, C10.2, C11.1, C12.1, C13.1, C14.1, C15.2, C16.1, C17.2, D1.1 (K), D2.1 (K), D3.1 (K), D4.1 (K), J1.4 (GND), J1.5 (Shield), J2.1, J3.1, J6.5 (GND), J6.6 (Shield), J8.1, J9.1, J10.1, J11.1, J12.1, J13.1, J15.1, J16.1, J17.1, J18.1, J19.1, J20.1, J21.3, J23.1, J24.1, J25.1, J26.1, SW1.2, U2.2 (VSS), U2.8 (STBY), U3.2 (GND), U4.5 (GND), U4.13 (GND), U5.2 (VSS), U5.8 (STBY), U6.7 (VSS), U6.20 (AVSS), U6.25 (VSS), U6.35 (VSS), U6.40 (VSS), U6.55 (VSS), U6.59 (VSS), U7.3 (VSS), U8.4 (VSS), Y1.2, Y1.4
unnamed: D1.2 (A), R1.1
unnamed: D2.2 (A), R4.1
unnamed: D3.2 (A), R5.1
unnamed: D4.2 (A), R6.1
unnamed: J1.2 (D-), J4.5
unnamed: J1.3 (D+), J4.6
unnamed: J4.1, J7.2
unnamed: J4.2, J7.1
unnamed: J5.1, R2.1
unnamed: J6.2 (D-), J7.4
unnamed: J6.3 (D+), J7.3
unnamed: J7.5, U4.8 (USBDP)
unnamed: J7.6, U4.9 (USBDM)
unnamed: J14.1, R3.1
unnamed: JP1.2 (B), U2.1 (TXD)
unnamed: JP2.2 (B), U2.4 (RXD)
unnamed: JP3.2 (B), U5.1 (TXD)
unnamed: JP4.2 (B), U5.4 (RXD)
unnamed: U8.2 (XT), Y1.3
unnamed: U8.3 (~XT), Y1.1

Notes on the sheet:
CAN1
MICRO CONTROLLER
PIC USB SELECT
USB SERIAL SELECT
UART SPI I2C
CAN2
MISO
MOSI
POWER
USB
24MHz

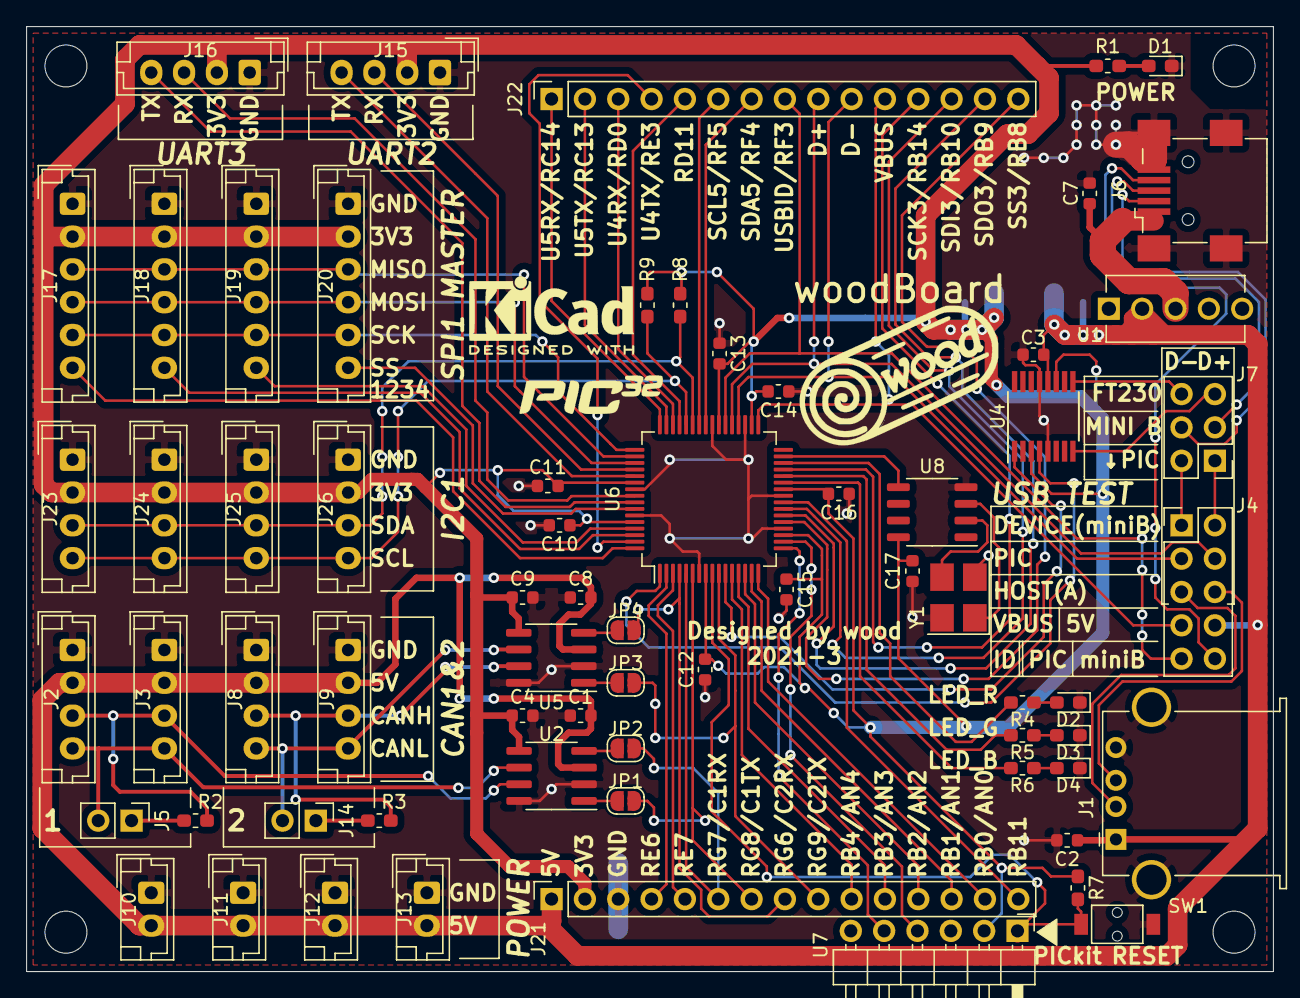
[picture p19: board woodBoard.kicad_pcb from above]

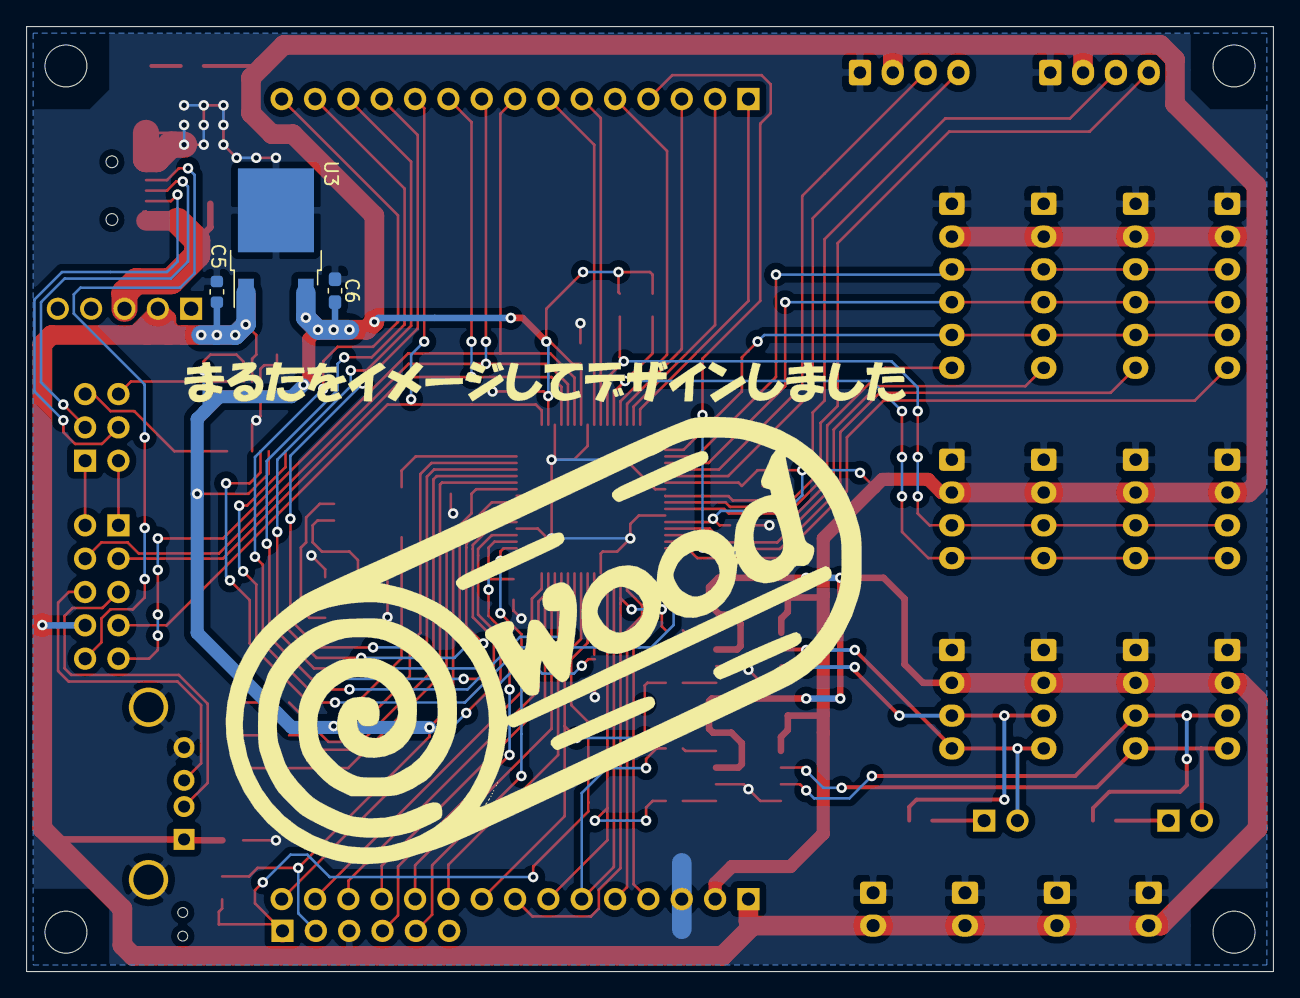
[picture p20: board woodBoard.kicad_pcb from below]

Board: 2 copper layers, 95.0 x 72.0 mm, 70 parts (3 on the bottom side), 78 nets.

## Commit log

2021-03-28 とりあえず基板完成のやつ
    [woodBoard.kicad_pcb, woodBoard.sch]
2021-03-28 部品表、部品個数表追加
    [部品個数表.csv, 部品表.csv]
2021-03-28 部品表ちょっと修正
    [部品表.csv]
2021-03-28 READMEにいろいろ書いた
2021-03-28 フォルダ構造変えた
    [部品個数表.csv, 部品表.csv]
2022-08-18 リポジトリの構造を複数のプロジェクトを入れれるようにした
    [woodBoard.kicad_pcb, woodBoard.sch, 部品個数表.csv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]
2022-08-18 電流制御モタドラwoodCurrentMD無印と2を追加した
    [woodCurrentMD.kicad_pcb, woodCurrentMD.sch, woodCurrentMD2.csv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]
2022-08-18 woodTerminal追加
    [woodTerminal.kicad_pcb, woodTerminal.sch]
2022-08-23 全体の説明
2022-08-23 woodBoardのkicad_wood_libがsubmoduleになってないのを直した
2022-08-27 雑にwoodCurrentMD2とwoodTerminalのreadme書いた、後で修正
2022-08-27 woodCurrentMDのreadmeを微小量かいた
2022-08-29 woodCurrentMD2の価格書いた
    [woodCurrentMD2個数表.csv]
2022-08-31 woodCurrentMD2のreadmeを修正
2022-09-05 woodBoardのミス説明とboothのURLを追加
2022-09-05 ファームウェアのリポジトリを一時的にkanojo_roboブランチに飛ばすようにした(こっちのほうが最新なので)
2022-09-22 woodTerminalの説明追加
    [ターミナル部品表.csv, ターミナル部品表個数表.csv]
2022-09-23 woodTerminalとwoodCurrentMD2のreadmeを修正
2022-09-23 woodTerminalの画像のリンク直し
